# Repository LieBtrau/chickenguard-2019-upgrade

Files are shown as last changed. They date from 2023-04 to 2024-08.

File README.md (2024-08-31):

# chickenguard-2019-upgrade

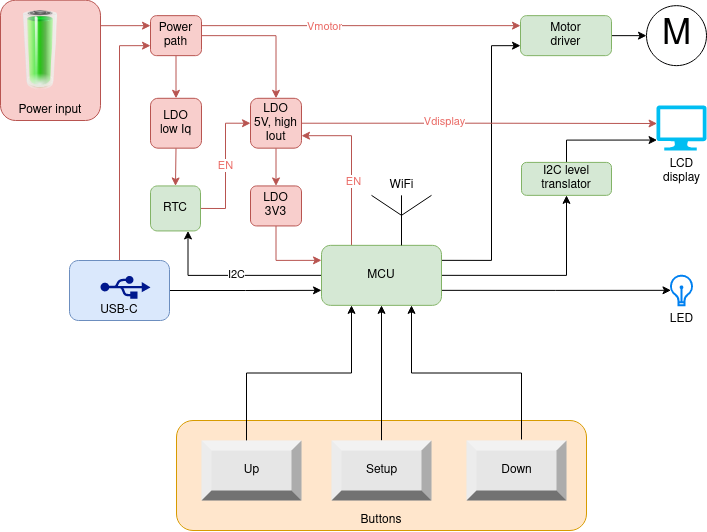
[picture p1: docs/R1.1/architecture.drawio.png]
architecture


Open-source replacement for the electronics of the [ChickenGuard](https://www.chickenguard.be/), an automatic chicken door opener.

## Added features, not present in original ChickenGuard
* Open source, so you can easily repair it yourself.  No epoxy covered PCBs.
* Will stop the door when blocked (e.g. by a chicken) (this feature is only present in most recent versions of the ChickenGuard).
* Automatic configuration of the door position.
* Web interface for configuration.
  * Time and date set automatically correctly from the smartphone.
  * Easy setup of fixed times for opening and closing the door.
  * Automatic setup of sunrise and sunset times, based on geolocation.
  * To save costs, the LCD display can be removed, and the device can be configured via the smartphone.
  * Future firmware upgrade might allow integration with home automation systems.
* USB-C port for power and programming.
* RoHS compliant (no CdS light sensor).

## [Use cases](./use-cases.md)

## Documentation

* [Product Requirement Document](./docs/PRD.md)

## Future work
The initial goal was to send the geolocation of the smartphone to the ESP32, so it can calculate the sunrise and sunset times.  That didn't work, because the ESP32 captive portal is not using HTTPS with a valid certificate.  The smartphone refuses to send the geolocation to an insecure website.

Instead of running a webserver on the ESP32.  Web Bluetooth (example [here](https://randomnerdtutorials.com/esp32-web-bluetooth/)) could be used.  The smartphone downloads a web page from the internet.  Using this info, the smartphone can connect to the ESP32 using Web Bluetooth.  Maybe that will allow the smartphone to send the geolocation to the ESP32. 

## Revision history
### Revision 1.02
  * [Schematic design](https://personal-viewer.365.altium.com/client/index.html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)
  * Patched PCB of 1.01.  No new PCB layout done

### Revision 1.01 : Using an external RTC
  * PCB cost reduction : layer count reduced from 4 to 2.
  * [Concept](./docs/R1.1/concept.md)
  * [Technical study](./docs/R1.1/technical-study_1.1.ipynb)
  * [Hardware design](https://365.altium.com/files/C9F51258-D859-4807-ACB1-E5928658F052) : for users with a free [AltiumLive account](https://365.altium.com/signin?ReturnUrl=https%3A%2F%2Fwww.altium.com%2Fviewer%2F).
  * [Hardware test report](./docs/R1.1/HardwareTest.ipynb)

### Revision 1.00 : Using the internal RTC of the ESP32
  * PCB design created, but never manufactured
  * [Concept](./docs/R1.0/concept.md)
  * [Technical study](./docs/R1.0/technical-study_1.0.ipynb)

## Prior Art
* [Peno64 ChickenGuard](https://github.com/peno64/ChickenGuard/blob/master/ChickenGuard.ino)
* [JP_chickenDoor](https://github.com/f2knpw/JP_chickenDoor/blob/master/JP_ESP32_ChickenDoor_wifi_IRsensor_Arduino.ino)
* [ChickenGuard](https://www.chickenguard.be/)
  * Uses an 8bit MCU (PIC18F14K22), an external RTC with 32.768kHz crystal and an SOIC8 motor driver.
  * The PCB was covered in epoxy, which has been removed using a hot air gun.  Some components got damaged in the process.  Aceton might also work (it should certainly work in case of hot glue).

---

Original version of this repository is at [LieBtrau/chickenguard-2019-upgrade](https://github.com/LieBtrau/chickenguard-2019-upgrade).

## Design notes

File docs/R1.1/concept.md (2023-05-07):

# Electronics
architecture

## Motor driver
MCU can't deliver enough current.  Added features such a measuring motor current.

## Power
### Battery
* 4xAA battery : cheap, readily available, easy to replace

### USB-C
* It will be used in 5V mode.  230V to USB-C adapter is readily available.

### Power path
This includes logic so that only one power source is active at a time.  No current can flow from one power source to the other.

### LDO low Iq
* Because the RTC can't directly be powered by the battery, a low Iq LDO is needed.

### LDO 5V, high current
* This LDO serves two purposes.  It is a pre-regulator for the 3V3-LDO, while at the same time providing 5V to the display.
* By only enabling the display when needed, a lot of power can be saved.

### 3V3 LDO to MCU
* The MCU can draw up to 350mA
* The LDO should have a low quiescent current (low Iq) while at the same time allowing for 350mA output current.
* Such an LDO typically has a low input voltage (<5.5V), so it can't be connected directly to the battery.  That's why the aforementioned LDOs are used.

## MCU
An MCU is needed with Wifi, RTC and low sleep currents.

## Display
The 16x2 display will be reused.  The display requires 5V to operate.

## I2C level translator
As the display needs 5V and it has a parallel interface, this would occupy lots of MCU-pins.  Moreover, a lot of level translators would be needed between the display and the MCU.  
Alternatively, an I²C-IO-expander will be used, powered from 5V.  Now, only the two I²C-lines need to be level translated.

## Buttons
3 standard momentary push buttons.

## LED
Single color red, or bicolor red-green

## RTC
* The ESP32 has an internal RTC, but it can only be enabled in ESP-IDF, not in PlatformIO.  This is a problem, as the ESP-IDF is not compatible with the Arduino framework and libraries.
* An external RTC comes to the rescue.

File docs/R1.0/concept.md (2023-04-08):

# Electronics
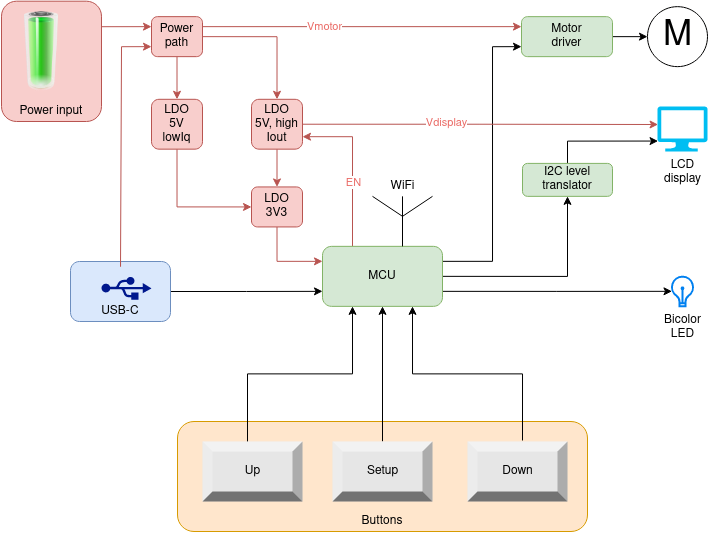
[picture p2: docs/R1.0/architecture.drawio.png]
architecture


## Motor driver
MCU can't deliver enough current.  Added features such a measuring motor current.

## Power
### Battery
* 4xAA battery : cheap, readily available, easy to replace

### USB-C
* It will be used in 5V mode.  230V to USB-C adapter is readily available.

### Power path
This includes logic so that only one power source is active at a time.  No current can flow from one power source to the other.

### LDO 5V, low Iq
* This is a pre-regulator for the 3V3-LDO.  Because it's always on, it needs a low quiescent current (Iq), about 1µA.
* The high input voltage range of this LDO protects the 3V3-LDO, which follows it.
* The output current of this low Iq LDO is limited, so it should only power the MCU while in sleep mode.  Once the MCU awakes, it should switch on the high-current LDO.

### LDO 5V, high current
* This LDO serves two purposes.  It is a pre-regulator for the 3V3-LDO, while at the same time providing 5V to the display.
* By only enabling the display when needed, a lot of power can be saved.

### 3V3 LDO to MCU
* The MCU can draw up to 350mA
* The LDO should have a low quiescent current (low Iq) while at the same time allowing for 350mA output current.
* Such an LDO typically has a low input voltage (<5.5V), so it can't be connected directly to the battery.  That's why the aforementioned LDOs are used.

## MCU
An MCU is needed with Wifi, RTC and low sleep currents.

## Display
The 16x2 display will be reused.  The display requires 5V to operate.

## I2C level translator
As the display needs 5V and it has a parallel interface, this would occupy lots of MCU-pins.  Moreover, a lot of level translators would be needed between the display and the MCU.  
Alternatively, an I²C-IO-expander will be used, powered from 5V.  Now, only the two I²C-lines need to be level translated.

## Buttons
3 standard momentary push buttons.

## LED
Single color red, or bicolor red-green

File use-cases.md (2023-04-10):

## Use case 1 : ChickenGuard, 2019 version no longer functions correctly
Replace original electronics with open source, easy-to-repair hardware.

## Use case 2 : Build it all yourself
1. Buy a chicken door 
  * [Self-locking](https://automatische-kippendeur-opener.nl/winkel/kippendeur/zelfsluitende-kippendeur-van-chickenguard/) : €49
  * [Standard](https://automatische-kippendeur-opener.nl/winkel/kippendeur/aluminium-kippendeur-met-2-geleiders/) : €20
2. Buy a DC-motor (€11)
  * Chickenguard uses the [SG-27063800-187K](https://www.alibaba.com/product-detail/SG-27-DC-gear-motor-gear_425835308.html) : €4/pce.  It's made by Ningbo Shengguang Motor Co. Ltd., Ningbo Leison Co. Ltd. (partnr. LS-SG27), ...    
  * [LS-25GA370-103](https://www.nbleisonmotor.com/LS-25GA370-Dc-Gear-Motor-pd6387204.html) has the same torque and voltage, but not the same dimensions.  This one might be easier available (e.g. [otronic](https://www.otronic.nl/nl/reductiemotor-6v-dc-77rpm-25ga-370.html))
3. Buy a housing (€10-€12)
  ChickenGuard uses a custom housing (85.5x121.2x60mm).  It's 153.5mm wide including the mounting bracket.
  * [Hammond 1555FF42GY](https://www.hammfg.com/files/parts/pdf/1555FF42GY.pdf) : 120x91x63mm, 161mm including mounting bracket
  * [Bopla XT 120805 WL 7035](https://www.bopla.de/en/enclosure-technology/euromas-x/abs-single-colour-with-wall-brackets/enclosure-abs-with-wall-brackets/xt-120805-wl-7035) : asymmetric PCB shape 
  * [Gainta G311MF](https://www.velleman.eu/downloads/20/infosheets/g311mf.pdf)
  * [Fibox 7083580](https://www.fibox.nl/catalog/1999/product/640/7083580_HOL1.html)

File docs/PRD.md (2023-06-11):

# Project information
| Party | ID |
|---|----|
| Participants | Me |
| Developer | Me |
| Stakeholders | My family |
| Target release date | 2023-05-01 |

The [ChickenGuard, 2019 version](https://www.youtube.com/watch?v=T8KP0sJ12n4), no longer functions correctly.  The motor only spins for a fraction of a second, and then stops.  The original electronics are covered in epoxy, and are not repairable.  
Instead of buying a new unit for a whopping €200, I will try to replace the electronics with open source, easy-to-repair hardware.

# Objective

Design a device that can pull-up and lower a chicken door, and that can be easily repaired.

# Assumptions, constraints
* The electronics need to fit in the current enclosure
* The geo-location of the device can be taken from the smartphone

# Dependencies

# Background & Strategic Fit
... Risk management

# Scope
The original design allows to control the door manually, based on sunlight and based on preset times.  These features should be present as well.

The original design requires to enter the time by pushing buttons.  This is not very user friendly.  
The device can be setup as webserver and controlled via a web interface.  Time and date can be taken from the smartphone.

The original design has a CdS light sensor, which is not RoHS compliant.  By combining the current time and date with the geolocation of the device.  The device can determine the sunrise and sunset time, and can open and close the door accordingly.  The geolocation can be taken from the smartphone, avoiding the need for a GPS module or the user having to enter the location manually. 

The current chickenguard has no clue how far the door is open.  There are no limit switches etc.  The user has to manually configure the top and bottom positions of the door.  This design will automatically detect door position based on the measured motor current.

The user might still wish to manually open and close the door.  This can be done via the push buttons.

# Product Features

## Enclosure
* PCB fits the current enclosure

### Installation
* easy to install and to remove.

## Electronics
* Two power options: through USB-jack or battery powered.
* minimum number of components

## Functionality
### Setup
1. After power on and when no config is present, the device act as wireless AP.  The user connects to the AP and as such automatically configures time and location of the device.
2. All parameters should be set from the web-interface.

### Button functionality
1. Central button : wakes up the web server
2. Buttons on either side of the central button are only for manual control of the door.

### LED functionality
1. Blink RED when power is low and battery needs to be replaced.
2. Optional : Blink GREEN when door is moving.

### Normal operation
Door opens/closes in three modes:
  * Mode 1 : user pushes up/down
  * Mode 2 : automatical by sunset, sunrise control
  * Mode 3 : automatical by preset time
Door must stop when it hits a chicken before the end of the travel.

# Release Criteria
...performance baseline

# Success Metrics
1. Solution accepted by partner

# Catalog Exclusions
* IoT integration

# Cost
* Less than €10 in BoM

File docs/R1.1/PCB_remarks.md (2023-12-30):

* 10µF caps should be 10V/0805
* bav170 assembled with bat54c
* ferrite bead 600ohm/1A assembled with 470ohm/1A
* bat54 single seems to have smaller package than sod-123.

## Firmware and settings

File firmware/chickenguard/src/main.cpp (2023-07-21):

/**
 */

#include "pins.h"
#include "Webservice.h"
#include <AsyncDelay.h>
#include "timeControl.h"
#include "NonVolatileStorage.h"
#include "i2c_hal.h"
#include "powerControl.h"
#include "motorControl.h"
#include "buttons.h"
#include "display.h"
#include "wifi_credentials.h"

static const char *TAG = "Main";

#ifdef ARDUINO_USB_MODE
#warning "USB mode enabled"
#endif

static void displayWifiCredentials();
static void webConfigDone();
static void updateTime(long utc, const String timezone);
static void setOpenDoorAlarm(NonVolatileStorage::DoorControl const doorControl);
static void setCloseDoorAlarm(NonVolatileStorage::DoorControl const doorControl);
static void handleButtonPress(ButtonReader::ButtonSelection buttonState);
static void powerOff();

static TimeControl timeControl(readBytes, writeBytes);
static NonVolatileStorage config;
static Webservice webserver(&config, updateTime, webConfigDone);
// Voltage divider scale = (R306+R309)/R309
static powerControl power(powerControl::BatteryTech::Alkaline, 4, 4.03);
static MotorControl motor(MOTOR_IN1, MOTOR_IN2, MOTOR_CURRENT_SENSE);
static AsyncDelay rtcPollingDelay;
static ButtonReader button(SNS_BUTTON);
static Display display;
static bool motorRunning = false;
static AsyncDelay batteryStatusDelay;

void setup()
{
    /**
     * Only needed for reading from serial port (either UART0 or USB CDC)
     * Reading : In ARDUINO_USB_MODE, the USB-CDC is used, otherwise UART0 is used.
     * For log writing :  data is always sent to both UART0 and USB CDC.
     */
    Serial.begin(115200);
    while (!Serial)
        ;
    ESP_LOGD(TAG, "\r\nBuild %s, utc: %lu\r\n", COMMIT_HASH, CURRENT_TIME);

    power.init();
    motor.init(power.getVoltage_mV());
    config.restoreAll();
    assert(i2c_hal_init(I2C_SDA, I2C_SCL));

    // Check if woken up by button press
    while (!button.isButtonStateStable())
    {
        delay(10);
    }
    ButtonReader::ButtonSelection buttonState = button.getButton();
    if (buttonState != ButtonReader::ButtonSelection::None)
    {

        handleButtonPress(buttonState);
    }

    display.init(delayMicroseconds);

    assert(timeControl.init(config.getTimeZone()));
    if (!timeControl.hasValidTime())
    {
        ESP_LOGE(TAG, "Time is not valid");
        // User will have to set the time using the webserver
        displayWifiCredentials();
        webserver.setup();
    }

    ESP_LOGD(TAG, "Ready to rumble");
    batteryStatusDelay.start(1000, AsyncDelay::MILLIS);
}

void loop()
{
    webserver.loop();
    if(batteryStatusDelay.isExpired())
    {
        batteryStatusDelay.repeat();
        //ESP_LOGI(TAG, "Battery voltage: %d mV", power.getVoltage_mV());
        webserver.notifyClients("battery", String(power.getVoltage_percent()) + String("%"));
    }
    power.run();

    // Handle alarms
    if (rtcPollingDelay.isExpired() && timeControl.hasValidTime())
    {
        rtcPollingDelay.start(1000, AsyncDelay::MILLIS);

        if (timeControl.openDoorAlarmTriggered())
        {
            setCloseDoorAlarm(config.getDoorControl());
            motor.openDoor();
        }
        else if (timeControl.closeDoorAlarmTriggered())
        {
            // Update the sunrise alarm
            setOpenDoorAlarm(config.getDoorControl());
            motor.closeDoor();
        }
    }
    if (button.update())
    {
        // Button state has changed
        handleButtonPress(button.getButton());
    }
    bool currentMotorRunning = motor.run();
    if (motorRunning && !currentMotorRunning)
    {
        // Motor has stopped
        ESP_LOGI(TAG, "Motor has stopped");
        powerOff();
    }
    motorRunning = currentMotorRunning;
}

void webConfigDone()
{
    ESP_LOGI(TAG, "Web config done");
    // Save all parameters
    config.saveAll();

    // Set the alarms
    setOpenDoorAlarm(config.getDoorControl());
    setCloseDoorAlarm(config.getDoorControl());

    powerOff();
}

void updateTime(long utc, const String timezone)
{
    ESP_LOGI(TAG, "Update time to UTC-seconds: %ld & timezone %s", utc, timezone.c_str());
    config.setTimeZone(timezone);
    timeControl.updateMcuTime(utc, timezone);
}

/**
 * @brief Program the alarm to open the door
 *
 * @param doorControl : controlled by sunrise/sunset or fix time
 */
void setOpenDoorAlarm(NonVolatileStorage::DoorControl const doorControl)
{
    switch (doorControl)
    {
    case NonVolatileStorage::DoorControl::SunriseSunset:
        float latitude, longitude;
        config.getGeoLocation(latitude, longitude);
        timeControl.setOpenAlarmSunrise(latitude, longitude);
        break;
    case NonVolatileStorage::DoorControl::FixTime:
        // Update needed, because the daylightsaving time might have changed
        // We have to adapt to daylight saving time, so do the chickens.
        uint8_t hr, min;
        config.getFixOpeningTime(hr, min);
        assert(timeControl.setOpenAlarmFixTime(hr, min));
        break;
    default:
        timeControl.disableAlarms();
        break;
    }
}

/**
 * @brief Program the alarm to close the door
 *
 * @param doorControl : controlled by sunrise/sunset or fix time
 */
void setCloseDoorAlarm(NonVolatileStorage::DoorControl const doorControl)
{
    switch (doorControl)
    {
    case NonVolatileStorage::DoorControl::SunriseSunset:
        float latitude, longitude;
        config.getGeoLocation(latitude, longitude);
        timeControl.setCloseAlarmSunset(latitude, longitude);
        break;
    case NonVolatileStorage::DoorControl::FixTime:
        // Update needed, because the daylightsaving time might have changed
        // We have to adapt to daylight saving time, so do the chickens.
        uint8_t hr, min;
        config.getFixClosingTime(hr, min);
        assert(timeControl.setCloseAlarmFixTime(hr, min));
        break;
    default:
        timeControl.disableAlarms();
        break;
    }
}

void handleButtonPress(ButtonReader::ButtonSelection buttonState)
{
    switch (buttonState)
    {
    case ButtonReader::ButtonSelection::Down:
        ESP_LOGI(TAG, "Button pressed: Down");
        motor.closeDoor();
        break;
    case ButtonReader::ButtonSelection::Up:
        ESP_LOGI(TAG, "Button pressed: Up");
        motor.openDoor();
        break;
    case ButtonReader::ButtonSelection::Standby:
        ESP_LOGI(TAG, "Button pressed: Start webserver");
        displayWifiCredentials();
        webserver.setup();
        break;
    case ButtonReader::ButtonSelection::None:
    default:
        // Button released
        break;
    }
}

void displayWifiCredentials()
{
    char ssid[16];
    sprintf(ssid, "SSID: %s", WIFI_SSID);
    char password[16];
    sprintf(password, "Pass: %s", WIFI_PASS);
    display.show(ssid, password);
}

void powerOff()
{
    ESP_LOGI(TAG, "Power off");
    display.off();
    power.powerOff();
}

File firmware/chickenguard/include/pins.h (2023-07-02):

#pragma once
#include "Arduino.h"

const int SNS_BUTTON = A2;
const int SNS_VMOTOR = A3;
const int MOTOR_CURRENT_SENSE = A4;
const int LED_PIN = 5;
const int MOTOR_IN1 = 6;
const int MOTOR_IN2 = 7;
const int I2C_SCL = 8;
const int I2C_SDA = 9;
const int EN_PWR = 10;

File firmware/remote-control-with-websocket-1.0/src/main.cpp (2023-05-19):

/**
 * ----------------------------------------------------------------------------
 * ESP32 Remote Control with WebSocket
 * ----------------------------------------------------------------------------
 * © 2020 Stéphane Calderoni
 * ----------------------------------------------------------------------------
 */

#include <SPIFFS.h>
#include <ESPAsyncWebServer.h>
#include <ArduinoJson.h>
#include "wifi_credentials.h"
#include "pins.h"
#include <DNSServer.h>

const IPAddress localIP(4, 3, 2, 1);          // the IP address the web server, Samsung requires the IP to be in public space
const IPAddress subnetMask(255, 255, 255, 0); // no need to change: https://avinetworks.com/glossary/subnet-mask/
const String localIPURL = "http://4.3.2.1";   // a string version of the local IP with http, used for redirecting clients to your webpage

DNSServer dnsServer;

// ----------------------------------------------------------------------------
// Definition of global constants
// ----------------------------------------------------------------------------

// Button debouncing
const uint8_t DEBOUNCE_DELAY = 10; // in milliseconds

// ----------------------------------------------------------------------------
// Definition of the LED component
// ----------------------------------------------------------------------------

struct Led
{
    // state variables
    uint8_t pin;
    bool on;

    // methods
    void update()
    {
        digitalWrite(pin, on ? HIGH : LOW);
    }
};

// ----------------------------------------------------------------------------
// Definition of the Button component
// ----------------------------------------------------------------------------

struct Button
{
    // state variables
    uint8_t pin;
    bool lastReading;
    uint32_t lastDebounceTime;
    uint16_t state;

    // methods determining the logical state of the button
    bool pressed() { return state == 1; }
    bool released() { return state == 0xffff; }
    bool held(uint16_t count = 0) { return state > 1 + count && state < 0xffff; }

    // method for reading the physical state of the button
    void read()
    {
        // reads the voltage on the pin connected to the button
        bool reading = digitalRead(pin);

        // if the logic level has changed since the last reading,
        // we reset the timer which counts down the necessary time
        // beyond which we can consider that the bouncing effect
        // has passed.
        if (reading != lastReading)
        {
            lastDebounceTime = millis();
        }

        // from the moment we're out of the bouncing phase
        // the actual status of the button can be determined
        if (millis() - lastDebounceTime > DEBOUNCE_DELAY)
        {
            // don't forget that the read pin is pulled-up
            bool pressed = reading == LOW;
            if (pressed)
            {
                if (state < 0xfffe)
                    state++;
                else if (state == 0xfffe)
                    state = 2;
            }
            else if (state)
            {
                state = state == 0xffff ? 0 : 0xffff;
            }
        }

        // finally, each new reading is saved
        lastReading = reading;
    }
};

// ----------------------------------------------------------------------------
// Definition of global variables
// ----------------------------------------------------------------------------

Led onboard_led = {8, false};
Led led = {LED_PIN, false};
Button button = {BTN_PIN, HIGH, 0, 0};

AsyncWebServer server(80); // HTTP port 80
AsyncWebSocket ws("/ws");

// ----------------------------------------------------------------------------
// SPIFFS initialization
// ----------------------------------------------------------------------------

void initSPIFFS()
{
    if (!SPIFFS.begin())
    {
        Serial.println("Cannot mount SPIFFS volume...");
        while (1)
        {
            onboard_led.on = millis() % 200 < 50;
            onboard_led.update();
        }
    }
}

// ----------------------------------------------------------------------------
// Connecting to the WiFi network
// ----------------------------------------------------------------------------

void initWiFi()
{
#ifdef WIFI_STATION
    WiFi.mode(WIFI_STA);
    WiFi.begin(WIFI_SSID, WIFI_PASS);
    Serial.printf("Trying to connect [%s] ", WiFi.macAddress().c_str());
    while (WiFi.status() != WL_CONNECTED)
    {
        Serial.print(".");
        delay(500);
    }
    Serial.printf(" %s\n", WiFi.localIP().toString().c_str());
#else
    WiFi.mode(WIFI_AP);                              // access point mode
    WiFi.softAPConfig(localIP, localIP, subnetMask); // IP address of the gateway should be the same as the local IP for captive portals
    WiFi.softAP(WIFI_SSID, WIFI_PASS);

    dnsServer.setTTL(300);             // set 5min client side cache for DNS
    dnsServer.start(53, "*", localIP); // if DNSServer is started with "*" for domain name, it will reply with provided IP to all DNS request
#endif
}

// ----------------------------------------------------------------------------
// Web server initialization
// ----------------------------------------------------------------------------

String processor(const String &var)
{
    return String(var == "STATE" && led.on ? "on" : "off");
}

void onRootRequest(AsyncWebServerRequest *request)
{
    AsyncWebServerResponse *response = request->beginResponse(SPIFFS, "/index.html", "text/html", false, processor);
    response->addHeader("Cache-Control", "public,max-age=31536000"); // save this file to cache for 1 year (unless you refresh)
    request->send(response);
}

void initWebServer()
{

    server.on("/favicon.ico", [](AsyncWebServerRequest *request)
              { request->send(404); }); // webpage icon

    // the catch all
    server.onNotFound([](AsyncWebServerRequest *request)
                      { request->redirect(localIPURL); });

    server.on("/", HTTP_ANY, onRootRequest);
    server.serveStatic("/", SPIFFS, "/");
    server.begin();
}

// ----------------------------------------------------------------------------
// WebSocket initialization
// ----------------------------------------------------------------------------

void notifyClients()
{
    const uint8_t size = JSON_OBJECT_SIZE(1);
    StaticJsonDocument<size> json;
    json["status"] = led.on ? "on" : "off";

    char buffer[17];
    size_t len = serializeJson(json, buffer);
    ws.textAll(buffer, len);
}
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

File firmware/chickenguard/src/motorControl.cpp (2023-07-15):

#include "motorControl.h"

static const char *TAG = "MotorControl";

MotorControl::MotorControl(uint8_t pinIn1, uint8_t pinIn2, uint8_t pinCurrentSense) : _pinIn1(pinIn1),
                                                                                      _pinIn2(pinIn2),
                                                                                      _pinCurrentSense(pinCurrentSense),
                                                                                      _currentSense(20)
{
}

MotorControl::~MotorControl()
{
}

void MotorControl::init(float motorVoltage)
{
    pinMode(_pinIn1, OUTPUT);
    pinMode(_pinIn2, OUTPUT);
    off();
    _AdcSamplingPeriod.start(50, AsyncDelay::MILLIS);
    ESP_LOGI(TAG, "Motor voltage: %f", motorVoltage);
    // Limits for current, in mA, measured at VMOTOR=4.5V
    RAISING_UNDERLOAD_CURRENT = limitConversion(1050, motorVoltage);
    RAISING_OVERLOAD_CURRENT = limitConversion(1700, motorVoltage);
    LOWERING_OVERLOAD_CURRENT = limitConversion(580, motorVoltage);
    NO_MOTOR_CURRENT = limitConversion(250, motorVoltage);
}

/**
 * @brief Run the motor
 *
 * @return true when motor is running, else false
 */
bool MotorControl::run()
{
    const unsigned long DEAD_TIME = 3000;
    const unsigned long RAISE_DOOR_TIME = 25000;
    const unsigned long LOWER_DOOR_TIME = 25000;
    const unsigned long LOOSE_ROPE_TIME = 5000;

    float current = 0;

    switch (_state)
    {
    case MotorState::Off:
        digitalWrite(_pinIn1, LOW);
        digitalWrite(_pinIn2, LOW);
        _motorOnTime.expire();
        return false;
    case MotorState::start_raise:
        digitalWrite(_pinIn1, LOW);
        digitalWrite(_pinIn2, HIGH);
        _motorOnTime.start(DEAD_TIME, AsyncDelay::MILLIS);
        _currentSense.clear();
        _direction = MotorDirection::Raise;
        _state = MotorState::dead_time;
        return true;
    case MotorState::start_lower:
        digitalWrite(_pinIn1, HIGH);
        digitalWrite(_pinIn2, LOW);
        _motorOnTime.start(DEAD_TIME, AsyncDelay::MILLIS);
        _currentSense.clear();
        _direction = MotorDirection::Lower;
        _state = MotorState::dead_time;
        return true;
    case MotorState::dead_time:
        // Wait for the motor to start and for the current to stabilize
        if (_motorOnTime.isExpired())
        {
            _motorOnTime.start((_direction == MotorDirection::Raise) ? RAISE_DOOR_TIME : LOWER_DOOR_TIME, AsyncDelay::MILLIS);
            _state = MotorState::running;
        }
        return true;
    case MotorState::raising_under_load:
        // Pull up loose rope until timeout or until the load is detected.
        if (_motorOnTime.isExpired())
        {
            // We won't be pulling up loose rope forever.
            _state = MotorState::Off;
        }
        if (readAdc(current))
        {
            ESP_LOGI(TAG, "Underload current: %2f < %2f", current, RAISING_UNDERLOAD_CURRENT);
        }
        if (current < NO_MOTOR_CURRENT)
        {
            ESP_LOGI(TAG, "No motor current detected: %2f < %2f", current, NO_MOTOR_CURRENT);
            _state = MotorState::Off;
        }
        if (current > RAISING_UNDERLOAD_CURRENT)
        {
            ESP_LOGI(TAG, "Underload condition ended");
            _motorOnTime.start(RAISE_DOOR_TIME, AsyncDelay::MILLIS);
            _state = MotorState::running;
        }
        return true;
    case MotorState::running:
        if (_motorOnTime.isExpired())
        {
            _state = MotorState::Off;
        }
        if (readAdc(current))
        {
            ESP_LOGI(TAG, "Current: %f", current);
        }
        if (current < NO_MOTOR_CURRENT)
        {
            ESP_LOGI(TAG, "No motor current detected: %2f < %2f", current, NO_MOTOR_CURRENT);
            _state = MotorState::Off;
        }
        if (current > RAISING_OVERLOAD_CURRENT)
        {
            ESP_LOGI(TAG, "Overload current detected: %2f > %2f", current, RAISING_OVERLOAD_CURRENT);
            _state = MotorState::Off;
        }
        if (_direction == MotorDirection::Raise && current < RAISING_UNDERLOAD_CURRENT)
        {
            // The motor is pulling up loose rope.
            ESP_LOGI(TAG, "Raising underload current detected: %2f < %2f", current, RAISING_UNDERLOAD_CURRENT);
            _motorOnTime.start(LOOSE_ROPE_TIME, AsyncDelay::MILLIS);
            _state = MotorState::raising_under_load;
        }
        if (_direction == MotorDirection::Lower && current > LOWERING_OVERLOAD_CURRENT)
        {
            ESP_LOGI(TAG, "Lowering overload current detected: %2f > %2f", current, LOWERING_OVERLOAD_CURRENT);
            _state = MotorState::Off;
        }
        return true;
    default:
        _state = MotorState::Off;
        return false;
    }
}

void MotorControl::openDoor()
{
    _state = MotorState::start_raise;
}

void MotorControl::closeDoor()
{
    _state = MotorState::start_lower;
}

void MotorControl::off()
{
    _state = MotorState::Off;
}

bool MotorControl::readAdc(float &current)
{
    if (_AdcSamplingPeriod.isExpired())
    {
        _AdcSamplingPeriod.start(50, AsyncDelay::MILLIS);
        _currentSense.addValue(analogRead(_pinCurrentSense));
        current = _currentSense.getAverage();
        return true;
    }
    return false;
}

void MotorControl::demo()
{
    ESP_LOGI(TAG, "Raise door");
    openDoor();
    while (run())
        ;
    ESP_LOGI(TAG, "Lower door");
    closeDoor();
    while (run())
        ;
    off();
}

/**
 * @brief Convert current limit from 4.5V to motor voltage
 * @details Measurements have shown that current at 6V is 20% higher than at 4.5V
 *  Let y be the limit at 4.5V
 *  Then the rico (a) is (1.2 * y - y) / (6V - 4.5V) = 0.2 * y / 1.5V = 2/15 * y
 *  And the new limit (x) is y + a * (Vmotor - 4.5V)
 * @param currentLimit4V5
 * @return float
 */
float MotorControl::limitConversion(float currentLimit4V5, float motorVoltage_mV)
{
    float rico = 0.133 * currentLimit4V5;
    float newLimit = currentLimit4V5 + rico * (motorVoltage_mV - 4500) * 1e-3f;
    ESP_LOGI(TAG, "Current limit at 4.5V: %2f mA, new limit: %2f", currentLimit4V5, newLimit);
    return newLimit;
}

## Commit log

2023-03-28 power architecture
2023-04-03 Add hardware WIP
    [LCD.SchDoc, MCU.SchDoc, chickenguard-upgrade.PrjPcb]
2023-04-03 Add ESP32-C3 reference manual
2023-04-08 Schematic ready
    [LCD.SchDoc, MCU.SchDoc, Main.SchDoc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]
2023-04-15 Place all PCB components
    [LCD.SchDoc, MCU.SchDoc, Main.SchDoc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]
2023-04-22 Design ready for review
    [LCD.SchDoc, MCU.SchDoc, Main.SchDoc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]
2023-04-24 PCB ordered
    [LCD.SchDoc, MCU.SchDoc, Main.SchDoc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]
2023-04-26 BoM cleanup
    [MCU.SchDoc, Motor.SchDoc, Power.SchDoc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]
2023-04-29 Parsing time with ESP32-C3
2023-04-29 Add 2nd source for dual row socket
2023-04-30 Update after first test with date-time on ESP32-C3
2023-05-10 KIPGRD E1.01
    [MCU.SchDoc, Main.SchDoc, Motor.SchDoc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]
2023-06-20 bug fix missing function definition
    [timeControl.cpp]
2023-06-22 Show battery level on the fly.
2023-06-24 Implement voltage monitor
2023-06-25 Rename voltageMonitor
2023-06-25 power monitor integration
2023-07-01 Add power measurement
2023-07-01 Adding motor test and momentary swich test
2023-07-01 motor control added
2023-07-02 Adding motor
2023-07-08 Add motor low load detection
2023-07-08 Add LCD with I2C control
2023-07-08 test digipot, lcd I2C, IO expander
2023-07-11 Add crystal test Add momentary switch improvement
2023-07-15 Test motor currents
2023-07-15 Major rework and bug fix
    [Webservice.cpp, buttons.cpp, display.cpp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]
2023-07-21 Print git commit ID at startup
2023-07-21 Add display power off control
2023-07-21 Testing power switchover
2023-07-23 Hardware E1.2
    [LCD.SchDoc, MCU.SchDoc, Main.SchDoc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]
2023-07-23 Add link to online schematic viewer
2023-07-23 Correct online schematic link
2023-12-30 Add latest changes
    [MCU.SchDoc, Motor.SchDoc, Power.SchDoc]
